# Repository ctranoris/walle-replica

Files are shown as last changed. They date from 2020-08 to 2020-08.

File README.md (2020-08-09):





# Wall-E Robot Replica
Robot and controller code for a Wall-E replica robot. For more information about the robot, visit https://wired.chillibasket.com/3d-printed-wall-e/
<br />
<br />

## Arduino Code (wall-e)
Main program to control the motors and servos of the robot. Features include:
1. An animation queue, keeping track of the next servo movements the robot needs to perform.
1. A random movement generator, allowing the robot to autonomously move and appear animated.
1. Velocity control of all servo motors, facilitating smooth accelerations and decelerations. 
1. Non-blocking serial parsing, allowing the movements of the robot to be remote controlled.
1. Battery level monitoring using a potential divider circuit.

## Raspberry Pi Web Server (web_interface)
The web interface is programmed in Python and uses *Flask* to generate a server. The Raspberry Pi is connected via USB to the Arduino micro-controller. The main features are:
1. A JavaScript joystick, with which the movement of the robot can easily be controller.
1. Manual control of all the servo motors.
1. A list of movement animations which can be performed by the robot.
1. A list of sounds which can be played.
1. Settings page, where motor parameters, sound volume, and video options can be modified.
1. Gamepad support; on any modern browsers, you can use a connected Xbox of PlayStation controller to control the robot.
1. A simple login page to prevent everyone from having access to the controls (note: this is not a full access control system, please don't use this web interface on untrusted/public networks)


*Image of the web interface and robot*
<br />
<br />

## Setup Instructions

### Arduino

#### Basic Installation
1. Ensure that the wiring of the electronics matches the diagram shown below.
1. Download/clone the folder "wall-e" from the GitHub repository.
1. Open `wall-e.ino` in the Arduino IDE; the files `animations.ino`, `MotorController.hpp` and `Queue.hpp` should automatically open on separate tabs of the IDE as well.
1. Install the `Adafruit_PWMServoDriver.h` library
	1. Go to Sketch -> Include Library -> Manage Libraries...
	1. Search for *Adafruit Servo*.
	1. Install latest version of the library.
1. Connect to the computer to the micro-controller with a USB cable. Ensure that the correct *Board* and *Port* are selected in the *Tools* menu.
1. Upload the sketch to the micro-controller.


*Diagram showing the wiring of the robot's electronic components*

#### Testing the Main Program
1. Once the sketch has been uploaded to the Arduino, power on the 12V battery while the micro-controller is still connected to the computer.
1. Open the *Serial Monitor* (button in top-right of Arduino IDE). Set the baud rate to 115200.
1. To control the movement of the robot, send the characters 'w', 'a', 's' or 'd' to move forward, left, back or right respectively. Send 'q' to stop all movement.
1. To move the head, send the characters 'j', 'l', 'i' or 'k' to tilt the head left or right and the eyes upwards or downwards. At this stage, the servos may try to move further than they should and may look uncoordinated. This will be solved by performing the servo motor calibration steps below.

#### Servo Motor Calibration
1. Download/clone the folder "wall-e_calibration" from the GitHub repository
1. Open `wall-e_calibration.ino` in the Arduino IDE.
1. Upload the sketch to the micro-controller, and open the serial monitor and set the baud rate to 115200.
1. The sketch is used to calibrate the maximum and minimum PWM pulse lengths required to move each servo motor across its desired range of motion. The standard LOW and HIGH positions of each of the servos can be seen on diagrams [on my website](https://wired.chillibasket.com/3d-printed-wall-e/). 
1. When starting the sketch and opening the serial monitor, the a message should appear after 2-3 seconds, saying that it is ready to calibrate the LOW position of the first servo motor (the head rotation).
1. Send the character 'a' and 'd' to move the motor backwards and forwards by -10 and +10. For finer control, use the characters 'z' and 'c' to move the motor by -1 and +1. 
1. Once the motor is position in the correct position, send the character 'n' to proceed to the calibration step. It will move on to the HIGH position of the same servo, after which the process will repeat for each of the 7 servos in the robot.
1. When all joints are calibrated, the sketch will output an array containing the calibration values to the serial monitor.
1. Copy the array, and paste it into lines 116 to 122 of the program *wall-e.ino*. The array should look similar to this:
    ```cpp
    int preset[][2] =  {{410,120},  // head rotation
                        {532,178},  // neck top
                        {120,310},  // neck bottom
                        {465,271},  // eye right
                        {278,479},  // eye left
                        {340,135},  // arm left
                        {150,360}}; // arm right
    ```

#### Battery Level Detection
When using batteries to power the robot, it is important to keep track of how much power is left. Some batteries may break if they are over-discharged, and the SD card of the Raspberry Pi may become corrupted if not enough power is delivered.
1. To use the battery level detection feature on the Arduino, connect the following resistors and wiring as shown in the image below. The resistors (potential divider) reduce the 12V voltage down to a value below 5V, which is safe for the Arduino to measure using its analogue pins. The recommended resistor values are `R1 = 100kÙ` and `R2 = 47kÙ`.
1. Uncomment line 50 in the main Arduino sketch *wall-e.ino*.
1. If you are using different resistor values, change the value of the potential divider gain factor on line 54 of the sketch, according to the formula: `POT_DIV = R2 / (R1 + R2)`. 
1. The program should now automatically check the battery level every 10 seconds, and this level will be shown on the Raspberry Pi web-interface in the "Status" section.


<br />
*Diagram showing the wiring of the battery level detection circuit*

#### Adding your own Servo Animations
My code comes with two animations which replicate scenes from the movie; the eye movement Wall-E does when booting-up, and a sequence of motions as Wall-E inquisitively looks around. From version 2.7 of the code, I've now made it easier to add your own servo motor animations so that you can make your Wall-E do other movements...
1. Open up the file `animations.ino`, which is located in the same folder as the main Arduino sketch. 
1. Each animation command consists of the positions you want each of the servo motors to move to, and the amount of time the animation should wait until moving on to the next instruction.
1. You can add a new animation by inserting an extra `case` section into the switch statement. You should slot you extra code into the space above the `default` section. For example:
    ```cpp
    case 3:
            // --- Title of your new motion sequence ---
            //          time,head,necT,necB,eyeR,eyeL,armL,armR
            queue.push({  12,  48,  40,   0,  35,  45,  60,  59});
            queue.push({1500,  48,  40,  20, 100,   0,  80,  80});
            // Add as many additional movements here as you need to complete the animation
            // queue.push({time, head rotation, neck top, neck bottom, eye right, eye left, arm left, arm right})
            break;
    ```
1. The time needs to be a number in milliseconds (for example, 3.5 seconds = 3500)
1. The servo motor position commands need to be an integer number between 0 to 100, where `0 = LOW` and `100 = HIGH` servo position as calibrated in the `wall-e_calibration.ino` sketch.
1. If you want to disable a motor for a specific move, you can use -1. 

<br />
<br />

### Raspberry Pi Web Server

#### Basic Installation
1. Setup the Raspberry Pi to run the latest version of Raspbian/NOOBS. The setup instructions can be found on the [Raspberry Pi website](https://www.raspberrypi.org/documentation/installation/installing-images/).
1. Open the command line terminal on the Raspberry Pi.
1. Ensure that the package list has been updated (this may take some time): `sudo apt-get update`
1. Install *Flask* - this is a Python framework used to create web servers:
    1. Ensure that pip is installed: `sudo apt-get install python-pip`
    1. Install Flask and its dependencies: `sudo pip install flask`
1. Clone repository into the home directory of the Raspberry Pi:
    ```shell
    cd ~
    git clone https://github.com/chillibasket/walle-replica.git
    ```
1. Set the web server password:
    1. Open *app.py*: `nano ~/walle-replica/web_interface/app.py` 
    1. On line 20 of *app.py* where is says `put_password_here`, insert the password you want to use for the web interface.
1. (Optional) Change the default audio directory and location of the script used to start/stop the video stream.
    1. If you followed the steps above exactly, there is no need to do this. However, if you want to move the web-interface files to a different directory on the Raspberry Pi, you will need to change the location where the program will look for the audio files.
    1. On line 23 of *app.py*, type the directory where the audio files are located. Ensure that the directory location ends with a forward slash: `/`.
    1. On line 22 of *app.py*, the location of the script used to start and stop the video camera stream can be modified.
1. Connect to the Arduino/micro-controller:
    1. Plug the Arduino/micro-controller into the USB port of the Raspberry Pi.
    1. If you would like the serial port used by the Arduino to be selected by default in the web-interface, you can set a preferred serial port device in the code. Go to line 21 of *app.py* and replace the text "ARDUINO" with the name of your device. The name must match the one which appears in the drop-down menu in the "Settings" tab of the web-interface.
    1. Press `CTRL + O` to save and `CTRL + X` to exit the nano editor.

#### Using the Web Server
1. To determine the current IP address of the Raspberry Pi on your network, type the command: `hostname -I`
1. To start the server: `python3 ~/walle-replica/web_interface/app.py`
1. To access the web interface, open a browser on any computer/device on the same network and type in the IP address of the Raspberry Pi, follow by `:5000`. For example `192.168.1.10:5000`
1. To stop the server press: `CTRL + C`
1. To start controlling the robot, you first need to start serial communication with the Arduino. To do this, go to the `Settings` tab of the web-interface, select the correct serial port from the drop-down list and press on the `Reconnect` button.

#### Adding a Camera Stream
1. Install *mjpg-streamer* - this is used to stream the video to the webserver. A good description of the installation procedure is [described here](https://github.com/cncjs/cncjs/wiki/Setup-Guide:-Raspberry-Pi-%7C-MJPEG-Streamer-Install-&-Setup-&-FFMpeg-Recording). Complete the *Install & Setup* steps, as well as creating the *Auto Start Manager Script*. Stop when you reach the *Start on Boot* section. 
1. Make sure that the manager script you created has the correct name and is in the correct directory: `/home/pi/mjpg-streamer.sh`. If you want the save the script in a different location, you need to update line 22 of *app.py*.
1. To make the script executable by the web-server, run this command in the terminal: `chmod +x /home/pi/mjpg-streamer.sh`

#### Automatically start Server on Boot
1. Create a `.service` file which is used to start the web interface: `nano ~/walle.service`
1. Paste the following text into the file:
    ```text
    [Unit]
    Description=Start Wall-E Web Interface
    After=network.target

    [Service]
    WorkingDirectory=/home/pi/walle-replica/web_interface
    ExecStart=/usr/bin/python3 app.py
    Restart=always
    StandardOutput=syslog
    StandardError=syslog
    SyslogIdentifier=walle
    User=pi

    [Install]
    WantedBy=multi-user.target
    ```
1. Press `CTRL + O` to save and `CTRL + X` to exit the nano editor.
1. Copy this file into the startup directory using the command: `sudo cp ~/walle.service /etc/systemd/system/walle.service`
1. To enable auto-start, use the following command: `sudo systemctl enable walle.service`
1. The web interface should now automatically start when the Raspberry Pi is turned on. You can also manually start and stop the service using the commands: `sudo systemctl start walle.service` and `sudo systemctl stop walle.service` 

#### Adding new Sounds
1. By default the Raspberry should automatically select whether to output audio to the HDMI port or the headphone jack. However, you can ensure that it always uses the headphone jack with the following command: `amixer cset numid=3 1`
1. Make sure that all the sound files you want to use are of type `*.ogg`. Most music/sound editors should be able to convert the sound file to this format.
1. Change the file name so that it has the following format: `[group name]_[file name]_[length in milliseconds].ogg`. For example: `voice_eva_1200.ogg`. In the web-interface, the audio files will be grouped using the "group name" and sorted alphabetically.
1. Upload the sound file to Raspberry Pi in the following folder: `~/walle-replica/web_interface/static/sounds/`
1. All the files should appear in the web interface when you reload the page. If the files do not appear, you may need to change the privileges required to access the folder: `sudo chmod -R 755 ~/walle-replica/web_interface/static/sounds`

#### Set up the Raspberry Pi as a WiFi hotspot
If you would like to control the robot outdoors or at conventions, there may not be any safe WiFi networks you can connect to. To overcome this issue and eliminate the need for any external networking equipment, the Raspberry Pi can broadcast its own WiFi network. You can then connect the computer/phone/tablet you are using to control the robot directly to this network.

The instructions for setting up such a WiFi hotspot can be found on [this website](https://thepi.io/how-to-use-your-raspberry-pi-as-a-wireless-access-point/). You only have to complete steps 1 to 5 for this project.
<br />
<br />

## Changelog

#### 7th August 2020 (Version 2.7)
1. Added a soft servo start function to the main Wall-E sketch and the servo calibration sketch. This prevents the servos from jumping as violently on startup.
1. Changed the data-type of the animation queue to reduce the amount of dynamic memory required. Also updated the Queue class so that the buffer memory can be declared globally; this means the compiler can keep track of how much memory the queue actually uses.
1. Moved the preset servo animations into a separate file, to make it easier to add your own animations. 

#### 20th June 2020
1. Minor bug fixes of the `Queue.hpp` and `MotoController.hpp` classes.
1. Updated commenting of code to make it more consistent.

#### 16th February 2020
1. Added gamepad support; any controller can now be used (such as the Xbox or PlayStation controllers) to puppet the robot.
1. Improved serial port handling; in the settings tab, all of the available serial ports are listed in a drop-down menu. 
1. New status indicators are now shown below the video stream. They visualise whether the Arduino and/or gamepad are connected.
1. Added support for battery level detection in both the Arduino code and the Raspberry Pi web interface.
1. Fixed the bug where the virtual joystick no longer worked properly when the window was resized.
1. Plus many other bug fixes!

#### 25th January 2020
1. Restructured the web-interface to make it display more nicely on mobile devices; fancy icons are now used!
1. Added manual servo control - this allows individual servos to be controlled directly from the web-interface.
1. Improved error handling - error messages are now consistently displayed in a pop-up at the bottom of the page.
1. Added instructions about how to automatically start server on boot to the Readme.

#### 31st October 2019
1. Fixed some bugs related to sound playback.
1. Added 2 sample sound files, which ensures that the sound directory is included in the git files.

#### 30th October 2019 
1. Added *wall-e_calibration.ino*, with which the maximum and minimum pulse widths of the servo motors can be calibrated.
1. Updated *wall-e.ino* to use relative coordinates rather than absolute servo pulse widths for the animation presets. This allows the servo calibration data to be used to ensure the movements are the same on all variants of the robot.

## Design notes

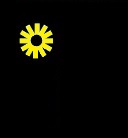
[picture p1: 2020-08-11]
web_interface/oled/bsun.jpg

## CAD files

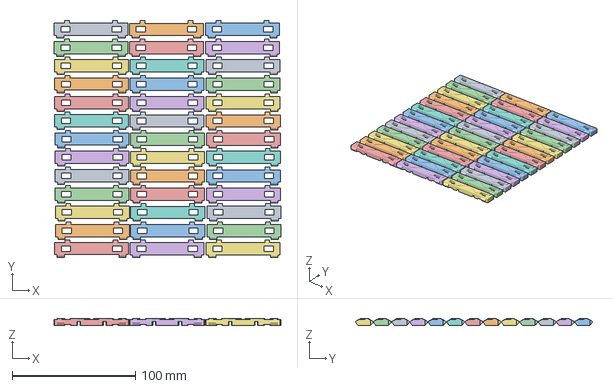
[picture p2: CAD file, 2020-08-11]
3dmodels/done/tread-plate-x70.3mf
183.8 x 191.9 x 6.00 mm
tread-plate-x70.stl x 39

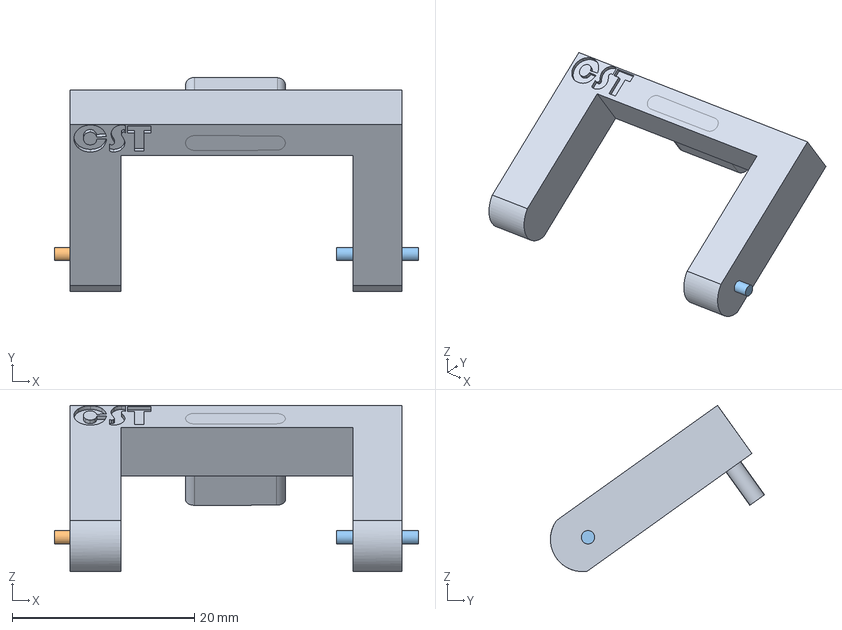
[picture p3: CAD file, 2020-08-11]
3dmodels/modifications/body-back-modified-hinge_02.FCStd
40.0 x 23.5 x 18.3 mm

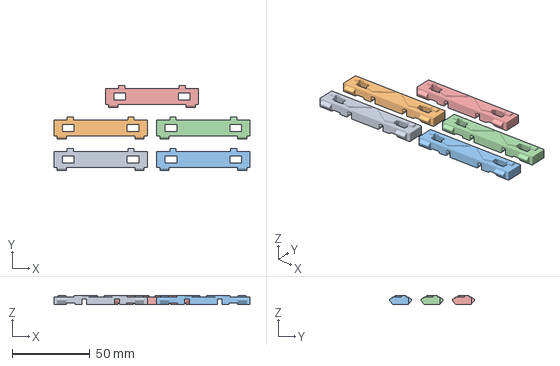
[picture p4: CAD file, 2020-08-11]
3dmodels/done/tread-plate-x5.3mf
126.0 x 54.7 x 6.00 mm
tread-plate-x70.stl x 5

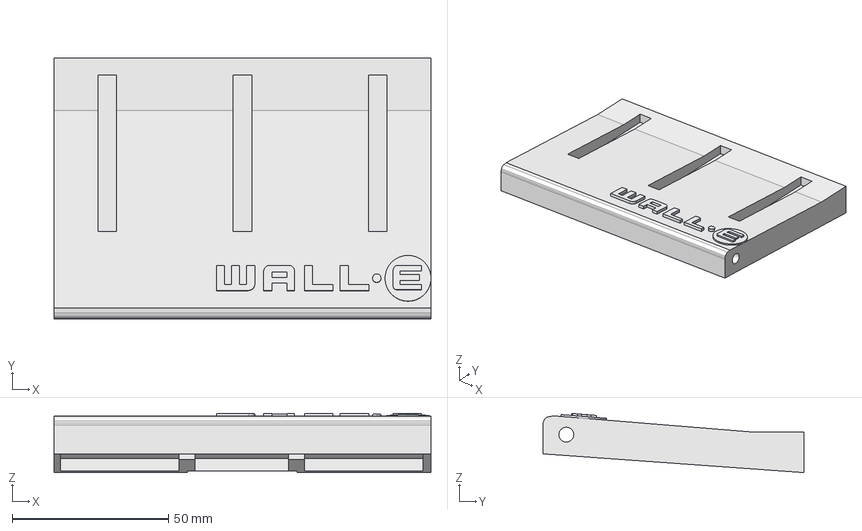
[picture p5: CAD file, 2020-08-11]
3dmodels/modifications/body-door-modified.FCStd
120.5 x 83.5 x 18.9 mm

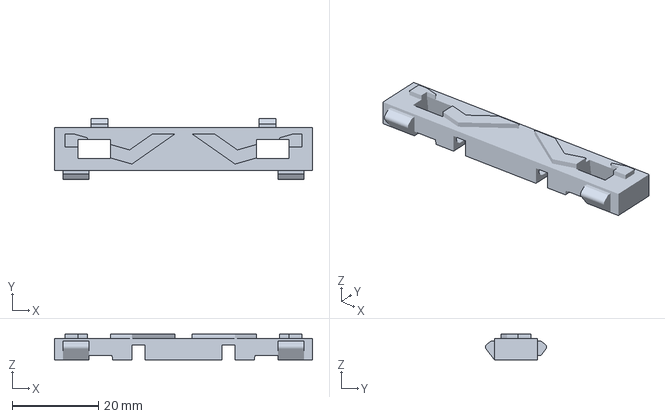
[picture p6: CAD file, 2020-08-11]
3dmodels/done/tread-plate-x1.3mf
60.0 x 14.2 x 6.00 mm

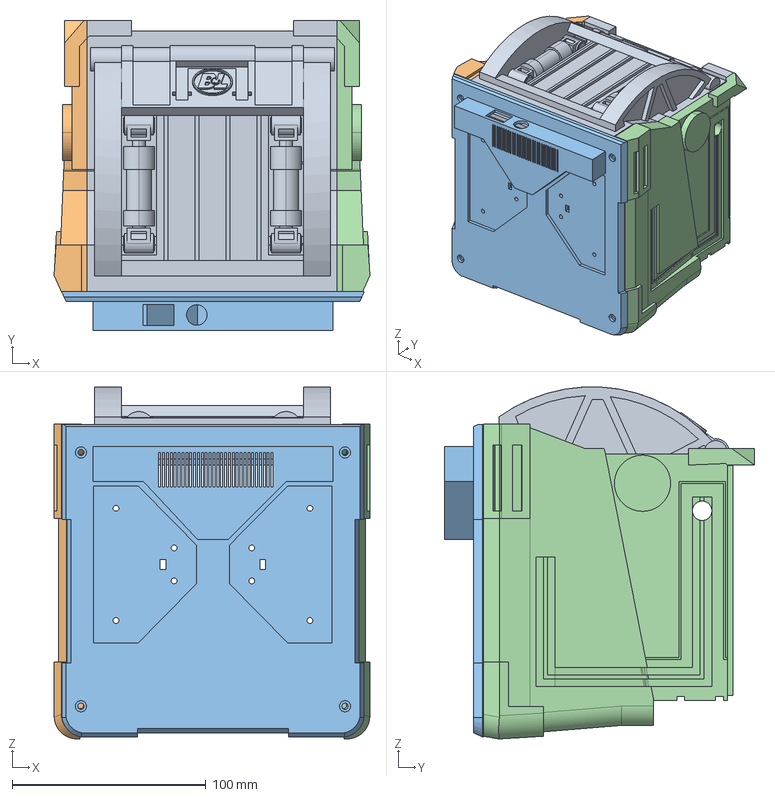
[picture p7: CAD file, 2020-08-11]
3dmodels/modifications/body-back-modified_03.FCStd
163.0 x 160.0 x 181.7 mm

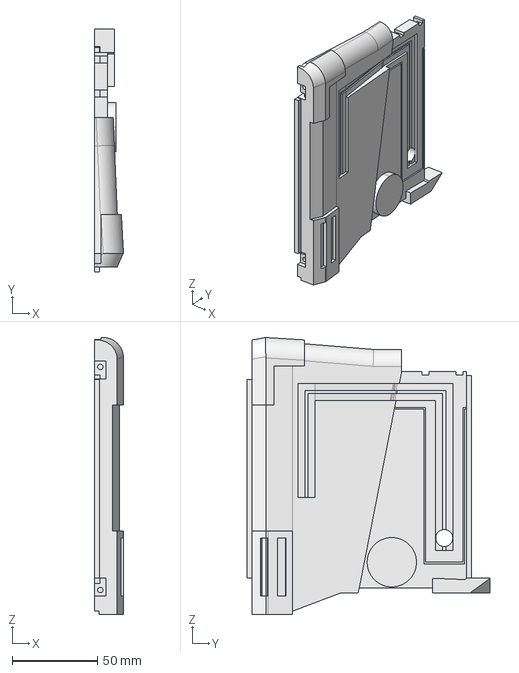
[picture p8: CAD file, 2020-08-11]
3dmodels/modifications/body-left-modified.FCStd
17.0 x 143.0 x 162.7 mm

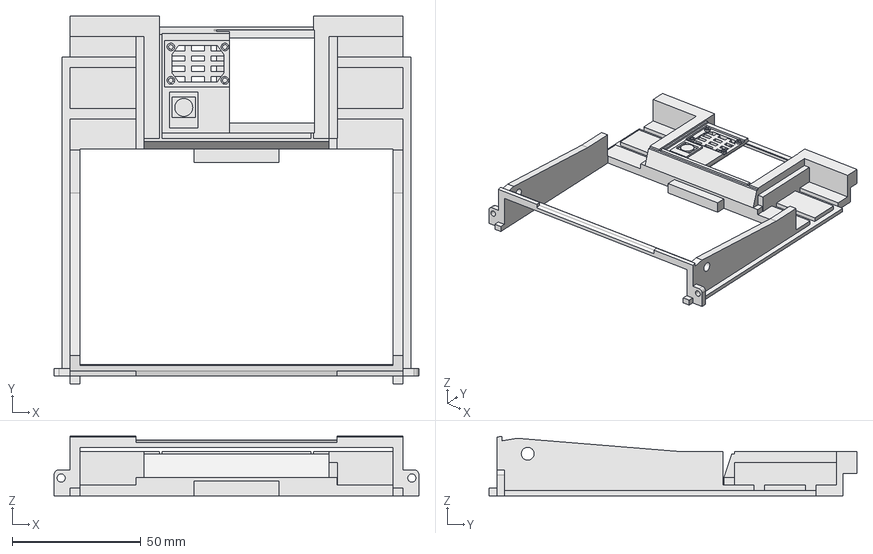
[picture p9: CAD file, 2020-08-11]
3dmodels/modifications/body-front-modified-2.FCStd
141.9 x 143.0 x 23.1 mm

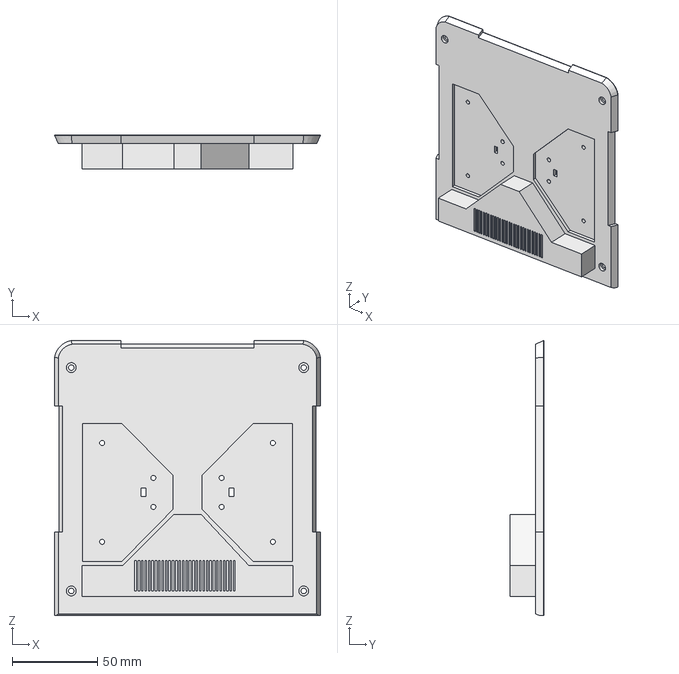
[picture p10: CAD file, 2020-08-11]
3dmodels/modifications/body-bottom-modified.FCStd
156.0 x 20.0 x 161.3 mm

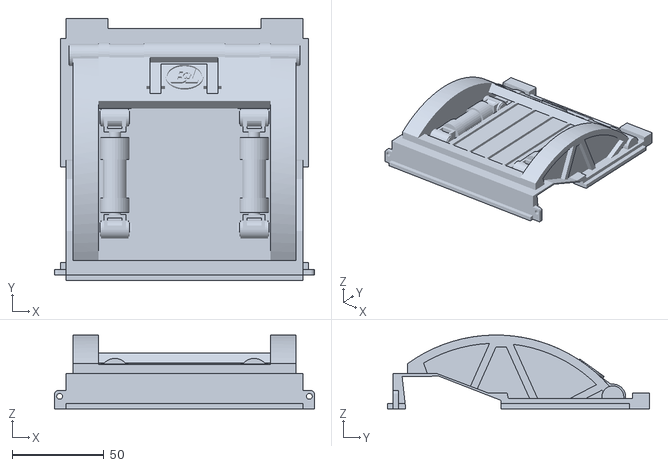
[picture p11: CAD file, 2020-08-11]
3dmodels/modifications/body-back-modified.stl
141.9 x 143.0 x 40.4

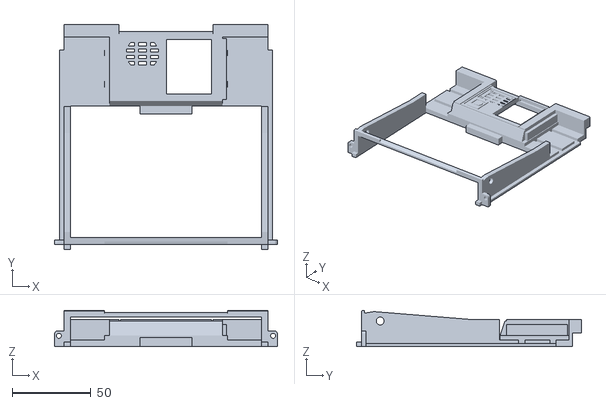
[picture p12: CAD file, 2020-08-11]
3dmodels/modifications/body-front-modified.stl
141.9 x 143.0 x 23.1

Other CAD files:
3dmodels/modifications/body-back-modified-hinge_03.stl
3dmodels/modifications/body-right-modified.FCStd
3dmodels/modifications/body-front-door-modified.stl
3dmodels/modifications/body-bottom-modified.stl
3dmodels/modifications/body-front-modified-2.stl
3dmodels/modifications/body-left-modified.stl
3dmodels/modifications/body-right-modified.stl

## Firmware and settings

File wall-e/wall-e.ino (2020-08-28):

/* WALL-E CONTROLLER CODE
 ********************************************
 * Code by: Simon Bluett
 * Email:   hello@chillibasket.com
 * Version: 2.7
 * Date:    7th August 2020
 ********************************************/

/* HOW TO USE:
 * 1. Install the Adafruit_PWMServoDriver library
 *    a. In the Arduino IDE, go to Sketch->Include Library->Manage Libraries
 *    b. Search for Adafruit PWM Library, and install the latest version
 * 2. Calibrate the servo motors, using the calibration sketch provided in the
 *    GitHub repository. Paste the calibrated values between line 116 to 122.
 * 3. Upload the sketch to the micro-controller, and open serial monitor at 
 *    a baud rate of 115200.
 * 4. Additional instructions and hints can be found at:
 *    https://wired.chillibasket.com/3d-printed-wall-e/
 */

#include <Wire.h>
#include <Adafruit_PWMServoDriver.h>
#include "Queue.hpp"
#include "MotorController.hpp"


// Define the pin-mapping
// -- -- -- -- -- -- -- -- -- -- -- -- -- --
#define DIR_L 12           // Motor direction pins
#define DIR_R 13
#define PWM_L  3           // Motor PWM pins
#define PWM_R 11
#define BRK_L  9           // Motor brake pins
#define BRK_R  8
#define SR_OE 10           // Servo shield output enable pin


// Battery level detection
// -- -- -- -- -- -- -- -- -- -- -- -- -- --
//
//   .------R1-----.-------R2------.     | The diagram to the left shows the  |
//   |             |               |     | potential divider circuit used by  |
// V_Raw     Analogue pin A2      GND    | the battery level detection system |
//
// The scaling factor is calculated according to ratio of the two resistors:
//   POT_DIV = R2 / (R1 + R2)
//   For example: 68000 / (90000 + 68000) = 0.4303
//
// To enable battery level detection, uncomment the next line:
#define BAT_L A2 			// Battery level detection analogue pin
#ifdef BAT_L
	#define BAT_MAX 11.1   // Maximum voltage
	#define BAT_MIN 8.8   // Minimum voltage
	#define POT_DIV 0.4303 // Potential divider scaling factor
#endif


// Define other constants
// -- -- -- -- -- -- -- -- -- -- -- -- -- --
#define FREQUENCY 10       // Time in milliseconds of how often to update servo and motor positions
#define SERVOS 9           // Number of servo motors (7 normal servos plus the two eyebrow servos)
#define THRESHOLD 1        // The minimum error which the dynamics controller tries to achieve
#define MOTOR_OFF 6000 	   // Turn servo motors off after 6 seconds
#define MAX_SERIAL 5       // Maximum number of characters that can be received
#define STATUS_TIME 10000  // Time in milliseconds of how often to check robot status (eg. battery level)


// Instantiate objects
// -- -- -- -- -- -- -- -- -- -- -- -- -- --
// Servo shield controller class - assumes default address 0x40
Adafruit_PWMServoDriver pwm = Adafruit_PWMServoDriver();

// Set up motor controller classes
MotorController motorL(DIR_L, PWM_L, BRK_L, false);
MotorController motorR(DIR_R, PWM_R, BRK_R, false);

// Queue for animations - buffer is defined outside of the queue
// class so that the compiler knows how much dynamic memory will be used
struct animation_t {
	uint16_t timer;
	int8_t servos[SERVOS]; 
};

#define QUEUE_LENGTH 40
animation_t buffer[QUEUE_LENGTH];
Queue <animation_t> queue(QUEUE_LENGTH, buffer);


// Motor Control Variables
// -- -- -- -- -- -- -- -- -- -- -- -- -- --
int pwmspeed = 255;
int moveVal = 0;
int turnVal = 0;
int turnOff = 0;


// Runtime Variables
// -- -- -- -- -- -- -- -- -- -- -- -- -- --
unsigned long lastTime = 0;
unsigned long animeTimer = 0;
unsigned long motorTimer = 0;
unsigned long statusTimer = 0;
unsigned long updateTimer = 0;
bool autoMode = false;


// Serial Parsing
// -- -- -- -- -- -- -- -- -- -- -- -- -- --
char firstChar;
char serialBuffer[MAX_SERIAL];
uint8_t serialLength = 0;


// ****** SERVO MOTOR CALIBRATION *********************
// Servo Positions:  Low,High
int preset[][2] =  {{618,362},  // head rotation
                    {645,148},  // neck top
                    {100,470},  // neck bottom
                    {265,330},  // eye right
                    {260,160},  // eye left
                    {600,375},  // arm left
                    {375,600}, // arm right
                    {290,170},  // eyebrow left
                    {450,460}}; // eyebrow right

// *****************************************************


// Servo Control - Position, Velocity, Acceleration
// -- -- -- -- -- -- -- -- -- -- -- -- -- --
// Servo Pins:	     0,   1,   2,   3,   4,   5,   6,   7,   8,   -,   -
// Joint Name:	  head,necT,necB,eyeR,eyeL,armL,armR,ebrL,ebrR,motL,motR
float curpos[] = { 248, 560, 140, 475, 270, 250, 290, 300, 300, 180, 180};  // Current position (units)
float setpos[] = { 248, 560, 140, 475, 270, 250, 290, 300, 300,   0,   0};  // Required position (units)
float curvel[] = {   0,   0,   0,   0,   0,   0,   0,   0,   0,   0,   0};  // Current velocity (units/sec)
float maxvel[] = { 500, 400, 500,2400,2400, 600, 600,1000,1000, 255, 255};  // Max Servo velocity (units/sec)
float accell[] = { 350, 300, 480,1800,1800, 500, 500,1200,1200, 800, 800};  // Servo acceleration (units/sec^2)



// ------------------------------------------------------------------
// 		INITIAL SETUP
// ------------------------------------------------------------------
void setup() {

	// Output Enable (EO) pin for the servo motors
	pinMode(SR_OE, OUTPUT);
	digitalWrite(SR_OE, HIGH);

	// Communicate with servo shield (Analog servos run at ~60Hz)
	pwm.begin();
	pwm.setPWMFreq(60);

	// Turn off servo outputs
	for (int i = 0; i < SERVOS; i++) pwm.setPin(i, 0);

	// Initialize serial communication for debugging
	Serial.begin(115200);
	Serial.println(F("--- Wall-E Control Sketch ---"));

	randomSeed(analogRead(0));

	// Check if servo animation queue is working, and move servos to known starting positions
	if (queue.errors()) Serial.println(F("Error: Unable to allocate memory for servo animation queue"));
	
	// Soft start the servo motors
	Serial.println(F("Starting up the servo motors"));
	digitalWrite(SR_OE, LOW);
	playAnimation(0);
	softStart(queue.pop(), 3500);

	Serial.println(F("Sartup complete; entering main loop"));
}


// -------------------------------------------------------------------
// 		READ INPUT FROM SERIAL
// -------------------------------------------------------------------
void readSerial() {
	// Read incoming byte
	char inchar = Serial.read();

	// If the string has ended, evaluate the serial buffer
	if (inchar == '\n' || inchar == '\r') {

		if (serialLength > 0) evaluateSerial();
		serialBuffer[0] = 0;
		serialLength = 0;

	// Otherwise add to the character to the buffer
	} else {
		if (serialLength == 0) firstChar = inchar;
		else {
			serialBuffer[serialLength-1] = inchar;
			serialBuffer[serialLength] = 0;
		}
		serialLength++;

		// To prevent overflows, evalute the buffer if it is full
		if (serialLength == MAX_SERIAL) {
			evaluateSerial();
			serialBuffer[0] = 0;
			serialLength = 0;
		}
	}
}


// -------------------------------------------------------------------
// 		EVALUATE INPUT FROM SERIAL
// -------------------------------------------------------------------
void evaluateSerial() {
	// Evaluate integer number in the serial buffer
	int number = atoi(serialBuffer);

	Serial.print(firstChar); Serial.println(number);

	// Motor Inputs and Offsets
	// -- -- -- -- -- -- -- -- -- -- -- -- -- --
	if      (firstChar == 'X' && number >= -100 && number <= 100) turnVal = int(number * 2.55); 		// Forward/reverse control
	else if (firstChar == 'Y' && number >= -100 && number <= 100) moveVal = int(number * 2.55); 		// Left/right control
	else if (firstChar == 'S' && number >=  100 && number <= 100) turnOff = number; 					// Steering offset
	else if (firstChar == 'O' && number >=    0 && number <= 250) curpos[9] = curpos[10] = int(number); 	// Motor deadzone offset

	// Animations
	// -- -- -- -- -- -- -- -- -- -- -- -- -- --
	else if (firstChar == 'A') playAnimation(number);

	// Autonomous servo mode
	// -- -- -- -- -- -- -- -- -- -- -- -- -- --
	else if (firstChar == 'M' && number == 0) autoMode = false;
	else if (firstChar == 'M' && number == 1) autoMode = true;

	// Manual servo control
	// -- -- -- -- -- -- -- -- -- -- -- -- -- --
	else if (firstChar == 'L' && number >= 0 && number <= 100) {   // Move left arm
		autoMode = false;
		queue.clear();
		setpos[5] = int(number * 0.01 * (preset[5][1] - preset[5][0]) + preset[5][0]);
	} else if (firstChar == 'R' && number >= 0 && number <= 100) { // Move right arm
		autoMode = false;
		queue.clear();
		setpos[6] = int(number * 0.01 * (preset[6][1] - preset[6][0]) + preset[6][0]);
	} else if (firstChar == 'B' && number >= 0 && number <= 100) { // Move neck bottom
		autoMode = false;
		queue.clear();
		setpos[2] = int(number * 0.01 * (preset[2][1] - preset[2][0]) + preset[2][0]);
	} else if (firstChar == 'T' && number >= 0 && number <= 100) { // Move neck top
		autoMode = false;
		queue.clear();
		setpos[1] = int(number * 0.01 * (preset[1][1] - preset[1][0]) + preset[1][0]);
	} else if (firstChar == 'G' && number >= 0 && number <= 100) { // Move head rotation
		autoMode = false;
		queue.clear();
		setpos[0] = int(number * 0.01 * (preset[0][1] - preset[0][0]) + preset[0][0]);
	} else if (firstChar == 'E' && number >= 0 && number <= 100) { // Move eye left
		autoMode = false;
		queue.clear();
		setpos[4] = int(number * 0.01 * (preset[4][1] - preset[4][0]) + preset[4][0]);
	} else if (firstChar == 'U' && number >= 0 && number <= 100) { // Move eye right
		autoMode = false;
		queue.clear();
		setpos[3] = int(number * 0.01 * (preset[3][1] - preset[3][0]) + preset[3][0]);
	} else if (firstChar == 'J' && number >= 0 && number <= 100) { // Move eyebrow left
		autoMode = false;
		queue.clear();
		setpos[7] = int(number * 0.01 * (preset[7][1] - preset[7][0]) + preset[7][0]);
	} else if (firstChar == 'K' && number >= 0 && number <= 100) { // Move eyebrow right
		autoMode = false;
		queue.clear();
		setpos[8] = int(number * 0.01 * (preset[8][1] - preset[8][0]) + preset[8][0]);
	}
	
	// Manual Movements with WASD
	// -- -- -- -- -- -- -- -- -- -- -- -- -- --
	else if (firstChar == 'w') {		// Forward movement
		moveVal = pwmspeed;
		turnVal = 0;
		setpos[0] = (preset[0][1] + preset[0][0]) / 2;
	}
	else if (firstChar == 'q') {		// Stop movement
		moveVal = 0;
		turnVal = 0;
		setpos[0] = (preset[0][1] + preset[0][0]) / 2;
	}
	else if (firstChar == 's') {		// Backward movement
		moveVal = -pwmspeed;
		turnVal = 0;
		setpos[0] = (preset[0][1] + preset[0][0]) / 2;
	}
	else if (firstChar == 'a') {		// Drive & look left
		moveVal = 0;
		turnVal = -pwmspeed;
		setpos[0] = preset[0][0];
	}
	else if (firstChar == 'd') {   		// Drive & look right
		moveVal = 0;
		turnVal = pwmspeed;
		setpos[0] = preset[0][1];
	}

	// Manual Eye Movements
	// -- -- -- -- -- -- -- -- -- -- -- -- -- --
	else if (firstChar == 'j') {		// Left head tilt
		setpos[4] = preset[4][0];
		setpos[3] = preset[3][1];
	}
	else if (firstChar == 'l') {		// Right head tilt
		setpos[4] = preset[4][1];
		setpos[3] = preset[3][0];
	}
	else if (firstChar == 'i') {		// Sad head
		setpos[4] = preset[4][0];
		setpos[3] = preset[3][0];
	}
	else if (firstChar == 'k') {		// Neutral head
		setpos[4] = int(0.4 * (preset[4][1] - preset[4][0]) + preset[4][0]);
		setpos[3] = int(0.4 * (preset[3][1] - preset[3][0]) + preset[3][0]);
	}
	
	// Manual Eyebrow Movements
	// -- -- -- -- -- -- -- -- -- -- -- -- -- --
	else if (firstChar == 'r') {		// Left eyebrow up
		setpos[7] = preset[7][1];
		setpos[8] = preset[8][0];
	}
	else if (firstChar == 't') {		// Both eyebrows up
		setpos[7] = preset[7][1];
		setpos[8] = preset[8][1];
	}
	else if (firstChar == 'y') {		// Both eyebrows down
		setpos[7] = preset[7][0];
		setpos[8] = preset[8][0];
	}
	else if (firstChar == 'u') {		// Right eyerbrow up
		setpos[7] = preset[7][0];
		setpos[8] = preset[8][1];
	}
	// Head movement
	// -- -- -- -- -- -- -- -- -- -- -- -- -- --
	else if (firstChar == 'f') {		// Head up
		setpos[1] = preset[1][0];
		setpos[2] = (preset[2][1] + preset[2][0])/2;
	}
	else if (firstChar == 'g') {		// Head forward
		setpos[1] = preset[1][1];
		setpos[2] = preset[2][0];
	}
	else if (firstChar == 'h') {		// Head down
		setpos[1] = preset[1][0];
		setpos[2] = preset[2][0];
	}
	
	// Arm Movements
	// -- -- -- -- -- -- -- -- -- -- -- -- -- --
	else if (firstChar == 'b') {		// Left arm low, right arm high
		setpos[5] = preset[5][0];
		setpos[6] = preset[6][1];
	}
	else if (firstChar == 'n') {		// Both arms neutral
		setpos[5] = (preset[5][0] + preset[5][1]) / 2;
		setpos[6] = (preset[6][0] + preset[6][1]) / 2;
	}
	else if (firstChar == 'm') {		// Left arm high, right arm low
		setpos[5] = preset[5][1];
		setpos[6] = preset[6][0];
	}
}


// -------------------------------------------------------------------
// 		SEQUENCE AND GENERATE ANIMATIONS
// -------------------------------------------------------------------
void manageAnimations() {
	// If we are running an animation
	// -- -- -- -- -- -- -- -- -- -- -- -- -- --
	if ((queue.size() > 0) && (animeTimer <= millis())) {
		// Set the next waypoint time
		animation_t newValues = queue.pop();
		animeTimer = millis() + newValues.timer;

		// Set all the joint positions
		for (int i = 0; i < SERVOS; i++) {
			// Scale the positions using the servo calibration values
			setpos[i] = int(newValues.servos[i] * 0.01 * (preset[i][1] - preset[i][0]) + preset[i][0]);
		}

	// If we are in autonomous mode, but there are no movements queued, generate new movements
	} else if (autoMode && (queue.size() < SERVOS+1) && (animeTimer <= millis())) {

		// For each of the servos
		for (int i = 0; i < SERVOS; i++) {

			// Randomly determine whether or not to update the servo
			if (random(2) == 1) {

				// For most of the servo motors
				if (i == 0 || i == 1 || i == 5 || i == 6) {

					// Randomly determine the new position
					unsigned int min = preset[i][0];
					unsigned int max = preset[i][1];
					if (min > max) {
						min = max;
						max = preset[i][0];
					}
					
					setpos[i] = random(min, max+1);

				// Since the eyes should work together, only look at one of them
				} else if (i == 3) {

					int midPos1 = int((preset[i][1] - preset[i][0])*0.4 + preset[i][0]);
					int midPos2 = int((preset[i+1][1] - preset[i+1][0])*0.4 + preset[i+1][0]);

					// Determine which type of eye movement to do
					// Both eye move downwards
					if (random(2) == 1) {
						setpos[i] = random(midPos1, preset[i][0]);
						float multiplier = (setpos[i] - midPos1) / float(preset[i][0] - midPos1);
						setpos[i+1] = ((1 - multiplier) * (midPos2 - preset[i+1][0])) + preset[i+1][0];

					// Both eyes move in opposite directions
					} else {
						setpos[i] = random(midPos1, preset[i][0]);
						float multiplier = (setpos[i] - preset[i][1]) / float(preset[i][0] - preset[i][1]);
						setpos[i+1] = (multiplier * (preset[i+1][1] - preset[i+1][0])) + preset[i+1][0];
					}
				}

			}
		}

		// Finally, figure out the amount of time until the next movement should be done
		animeTimer = millis() + random(500, 3000);

	}
}


// -------------------------------------------------------------------
// 		MANAGE THE MOVEMENT OF THE SERVO MOTORS
// -------------------------------------------------------------------
void manageServos(float dt) {
	// SERVO MOTORS
	// -  -  -  -  -  -  -  -  -  -  -  -  -
	bool moving = false;
	for (int i = 0; i < SERVOS; i++) {

		float posError = setpos[i] - curpos[i];

		// If position error is above the threshold
		if (abs(posError) > THRESHOLD && (setpos[i] != -1)) {

			digitalWrite(SR_OE, LOW);
			moving = true;

			// Determine motion direction
			bool dir = true;
			if (posError < 0) dir = false;

			// Determine whether to accelerate or decelerate
			float acceleration = accell[i];
			if ((curvel[i] * curvel[i] / (2 * accell[i])) > abs(posError)) acceleration = -accell[i];

			// Update the current velocity
			if (dir) curvel[i] += acceleration * dt / 1000.0;
			else curvel[i] -= acceleration * dt / 1000.0;

			// Limit Velocity
			if (curvel[i] > maxvel[i]) curvel[i] = maxvel[i];
			if (curvel[i] < -maxvel[i]) curvel[i] = -maxvel[i];
			
			float dP = curvel[i] * dt / 1000.0;

			if (abs(dP) < abs(posError)) curpos[i] += dP;
			else curpos[i] = setpos[i];

			pwm.setPWM(i, 0, curpos[i]);

		} else {
			curvel[i] = 0;
		}
	}

	// Disable servos if robot is not moving
	// This prevents the motors from overheating
	if (moving) motorTimer = millis() + MOTOR_OFF;
	else if (millis() > motorTimer) {
		//digitalWrite(SR_OE, HIGH);
		for (int i = 0; i < SERVOS; i++) {
			pwm.setPin(i, 0);
		}
	}
}


// -------------------------------------------------------------------
// 		SOFT START - Try and start up servo gently
// -------------------------------------------------------------------
void softStart(animation_t targetPos, int time) {

	for (int i = 0; i < SERVOS; i++) {
		if (targetPos.servos[i] >= 0) {
			curpos[i] = int(targetPos.servos[i] * 0.01 * (preset[i][1] - preset[i][0]) + preset[i][0]);

			unsigned long endTime = millis() + time / SERVOS;

			while (millis() < endTime) {
				 pwm.setPWM(i, 0, curpos[i]);
				delay(10);
				pwm.setPin(i, 0);
				delay(50);
			}
			pwm.setPWM(i, 0, curpos[i]);
			setpos[i] = curpos[i];
		}
	}
}


// -------------------------------------------------------------------
// 		MANAGE THE MOVEMENT OF THE MAIN MOTORS
// -------------------------------------------------------------------
void manageMotors(float dt) {
	// Update Main Motor Values
	setpos[9] = moveVal - turnVal - turnOff;
	setpos[10] = moveVal + turnVal + turnOff;

	// MAIN DRIVING MOTORS
	// -  -  -  -  -  -  -  -  -  -  -  -  -
	for (int i = SERVOS; i < SERVOS + 2; i++) {

		float velError = setpos[i] - curvel[i];

		// If velocity error is above the threshold
		if (abs(velError) > THRESHOLD && (setpos[i] != -1)) {

			// Determine whether to accelerate or decelerate
			float acceleration = accell[i];
			if (setpos[i] < curvel[i] && curvel[i] >= 0) acceleration = -accell[i];
			else if (setpos[i] < curvel[i] && curvel[i] < 0) acceleration = -accell[i]; 
			else if (setpos[i] > curvel[i] && curvel[i] < 0) acceleration = accell[i];

			// Update the current velocity
			float dV = acceleration * dt / 1000.0;
			if (abs(dV) < abs(velError)) curvel[i] += dV;
			else curvel[i] = setpos[i];
		} else {
			curvel[i] = setpos[i];
		}
		
		// Limit Velocity
		if (curvel[i] > maxvel[i]) curvel[i] = maxvel[i];
		if (curvel[i] < -maxvel[i]) curvel[i] = -maxvel[i];
	}

	// Update motor speeds
	motorL.setSpeed(curvel[SERVOS]);
	motorR.setSpeed(curvel[SERVOS+1]);
}


// -------------------------------------------------------------------
// 		BATTERY LEVEL DETECTION
// -------------------------------------------------------------------
#ifdef BAT_L
void checkBatteryLevel() {

	// Read the analogue pin and calculate battery voltage
	float voltage = analogRead(BAT_L) * 5 / 1024.0;
 //Serial.print(F("voltage")); Serial.println(voltage);
	voltage = voltage / POT_DIV;
	int percentage = int(100 * (voltage - BAT_MIN) / float(BAT_MAX - BAT_MIN));

	// Send the percentage via serial
 Serial.print(F("Battery_")); Serial.println(percentage);
 //Serial.print(F("voltage")); Serial.println(voltage);
 
}
#endif


// -------------------------------------------------------------------
// 		MAIN PROGRAM LOOP
// -------------------------------------------------------------------
void loop() {

	// Read any new serial messages
	// -- -- -- -- -- -- -- -- -- -- -- -- -- --
	if (Serial.available() > 0){
		readSerial();
	}


	// Load or generate new animations
	// -- -- -- -- -- -- -- -- -- -- -- -- -- --
	manageAnimations();


	// Move Servos and wheels at regular time intervals
	// -- -- -- -- -- -- -- -- -- -- -- -- -- --
	if (updateTimer < millis()) {
		updateTimer = millis() + FREQUENCY;

		unsigned long newTime = micros();
		float dt = (newTime - lastTime) / 1000.0;
		lastTime = newTime;

		manageServos(dt);
		manageMotors(dt);
	}


	// Update robot status
	// -- -- -- -- -- -- -- -- -- -- -- -- -- --
	if (statusTimer < millis()) {
		statusTimer = millis() + STATUS_TIME;

		#ifdef BAT_L
			checkBatteryLevel();
		#endif
	}
}

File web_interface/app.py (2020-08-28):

#############################################
# Robot Webinterface - Python Script
# Simon Bluett, https://wired.chillibasket.com
# V1.4, 16th February 2020
#############################################

from flask import Flask, request, session, redirect, url_for, jsonify, render_template
import queue 		# for serial command queue
import threading 	# for multiple threads
import os
import pygame		# for sound
import serial 		# for Arduino serial access
import serial.tools.list_ports
import subprocess 	# for shell commands


#--------------Driver Library-----------------#
import RPi.GPIO as GPIO
import OLED_Driver as OLED
#--------------Image Library---------------#
from PIL  import Image
from PIL import ImageDraw
from PIL import ImageFont
from PIL import ImageColor
#-------------Test Display Functions---------------#
import sys
import cv2
import numpy as np
import time

import gtts


import getopt
import scipy.io.wavfile as wavfile
import math
import sys
import pydub 
from waveshaper import Waveshaper

app = Flask(__name__)


##### VARIABLES WHICH YOU CAN MODIFY #####
loginPassword = "12345"                                  # Password for web-interface
arduinoPort = "ARDUINO"                                              # Default port which will be selected
streamScript = "/home/pi/mjpg-streamer.sh"                           # Location of script used to start/stop video stream
soundFolder = "/home/pi/walle-replica/web_interface/static/sounds/"  # Location of the folder containing all audio files
oledFolder = "/home/pi/walle-replica/web_interface/oled/"  # Location of the folder containing all audio files
app.secret_key = os.environ.get("SECRET_KEY") or os.urandom(24)      # Secret key used for login session cookies


#-------------OLED-----------------#
WIDTH = 128
HEIGHT = 128 # Change to 32 depending on your screen resolution
##########################################



#------------ Constants for robot VOICE-----------------#
# Diode constants (must be below 1; paper uses 0.2 and 0.4)
VB = 0.01
VL = 0.02
# Controls distortion
H = 1
# Controls N samples in lookup table; probably leave this alone
LOOKUP_SAMPLES = 1024
# Frequency (in Hz) of modulating frequency
MOD_F = 50


# Start sound mixer
pygame.mixer.init()

# Set up runtime variables and queues
exitFlag = 0
arduinoActive = 0
streaming = 0
volume = 5
batteryLevel = -999
queueLock = threading.Lock()
workQueue = queue.Queue()
threads = []
videothreads = []
videoFlag = 0
stopVideo = 0
#############################################
# Set up the multithreading stuff here
#############################################
# The second thread will be used to send data to the Arduino
class arduino (threading.Thread):
	def __init__(self, threadID, name, q, port):
		threading.Thread.__init__(self)
		self.threadID = threadID
		self.name = name
		self.q = q
		self.port = port
	def run(self):
		print("Starting Arduino Thread", self.name)
		process_data(self.name, self.q, self.port)
		print("Exiting Arduino Thread", self.name)

# Function to send data to the Arduino from a buffer queue
def process_data(threadName, q, port):
	global exitFlag
	
	ser = serial.Serial(port,115200)
	ser.flushInput()
	dataString = ""
	while not exitFlag:
		try:
			queueLock.acquire()
			if not workQueue.empty():
				data = q.get() + '\n'
				queueLock.release()
				ser.write(data.encode())
				print(data)
			else:
				queueLock.release()
			if (ser.inWaiting() > 0):
				data = ser.read()
				if (data.decode() == '\n' or data.decode() == '\r'):
					print(dataString)
					parseArduinoMessage(dataString)
					dataString = ""
				else:
					dataString += data.decode()
			if (videoFlag == 1):
				print("A video is already active,sleeping queue")
				time.sleep(0.100)
		# If an error occured in the Arduino Communication
		except Exception as e: 
			print(e)
			exitFlag = 1
	ser.close()

# Function to parse messages received from the Arduino
def parseArduinoMessage(dataString):
	global batteryLevel
	
	# Battery level message
	if "Battery" in dataString:
		dataList = dataString.split('_')
		
		print("len(dataList)=" + str(len(dataList)) )
		try:
			int(dataList[1])
			is_dig = True
		except ValueError:
			is_dig = False

		if len(dataList) > 1 and is_dig:
			batteryLevel = dataList[1]
			DisplayBatteryLevel();

# Turn on/off the Arduino Thread system
def onoff_arduino(q, portNum):
	global arduinoActive
	global exitFlag
	global threads
	global batteryLevel
	
	if not arduinoActive:
		# Set up thread and connect to Arduino
		exitFlag = 0

		usb_ports = [
			p.device
			for p in serial.tools.list_ports.comports()
		]
		
		thread = arduino(1, "Arduino", q, usb_ports[portNum])
		thread.start()
		threads.append(thread)

		arduinoActive = 1

	else:
		# Disconnect Arduino and exit thread
		exitFlag = 1
		batteryLevel = -999

		# Clear the queue
		queueLock.acquire()
		while not workQueue.empty():
			q.get()
		queueLock.release()

		# Join any active threads up
		for t in threads:
			t.join()

		threads = []
		arduinoActive = 0

	return 0


# Test whether the Arduino connection is still active
def test_arduino():
	global arduinoActive
	global exitFlag
	global workQueue
	
	if arduinoActive and not exitFlag:
		return 1
	elif exitFlag and arduinoActive:
		onoff_arduino(workQueue, 0)
	else:
		return 0


# Turn on/off the MJPG Streamer
def onoff_streamer():
	global streaming
	
	if not streaming:
		# Turn on stream
		subprocess.call([streamScript, 'start'], stdout=subprocess.DEVNULL, stderr=subprocess.STDOUT)
		result = ""
		# Check whether the stream is on or not
		try:
			result = subprocess.run([streamScript, 'status'], stdout=subprocess.PIPE).stdout.decode('utf-8')
		except subprocess.CalledProcessError as e:
			result = e.output.decode('utf-8')
		print(result)
		
		if 'stopped' in result:
			streaming = 0
			return 1
		else:
			streaming = 1
			return 0

	else:
		# Turn off stream
		subprocess.call([streamScript, 'stop'], stdout=subprocess.DEVNULL, stderr=subprocess.STDOUT)
		
		streaming = 0
		return 0


#############################################
# Flask Pages and Functions
#############################################
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

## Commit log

2020-08-03 oled driver
2020-08-11 replace calibration values
2020-08-11 added models
    [body-back-modified-hinge_02.FCStd, body-back-modified-hinge_03.stl, body-back-modified.stl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]
2020-08-11 initializing battery level, adding videos
2020-08-11 fix batteryLevel
2020-08-11 battery level
2020-08-12 fix min voltage
2020-08-23 try thread
2020-08-28 battery level fix

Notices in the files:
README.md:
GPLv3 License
